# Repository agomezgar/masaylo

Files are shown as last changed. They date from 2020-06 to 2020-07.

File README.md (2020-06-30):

# Robot educativo Masaylo
Estoy intentando desarrollar un robot compatible con Arduino impreso en 3D, Masaylo, de tipo Low-Cost, propulsado por motores DC de los típicos que podemos encontrar en cualquier Aula-Taller de Tecnología.
A medida que progresemos intentaremos dotar al proyecto de una estructura algo más modular y coherente.

## Apariencia general

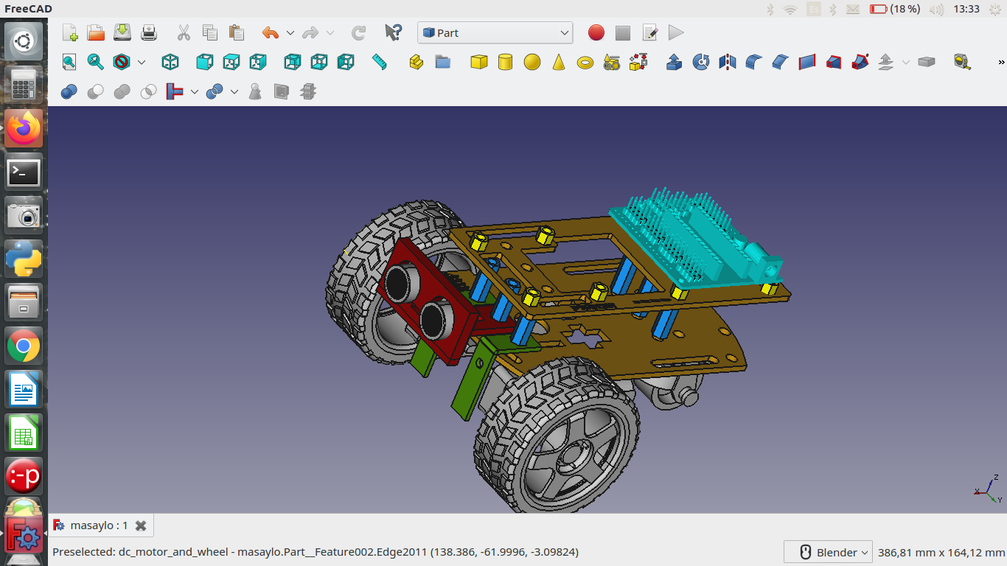
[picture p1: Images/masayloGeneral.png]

Utilizaremos: un Arduino nano con su correspondiente shield de expansión, un módulo L298N para gobernar dos motores DC, una rueda loca de 25x13 cm (o similar), un módulo sensor de ultrasonidos de tipo HC-SR04, dos sensores de infrarrojos de tipo FC-51 y un módulo BT modelo HC-05 o HC-06 que posiblemente habrá que tunear mediante comandos AT (o no; lo fundamental es saber a qué velocidad vamos a comunicarnos con él, y el código original espera que trabajemos a 19200 baudios; si es más cómodo para vosotros, podéis modificar el código para que trabaje a 9600 baudios).

## BOM (Bill of Materials; qué necesitamos)
La lista de objetos impresos en 3D, electrónica y tornillería varia la he dejado en el documento BOM.md que tenéis en la raíz del repositorio

## Instrucciones de montaje
El montaje mecánico del robot es relativamente sencillo. Se incluyen todas las indicaciones en el documento Montaje

## Conexionado/pinout
El Masaylo es lo suficientemente sencillo para que el profe de Tecnología o aficionado a la Robótica elija su propio conexionado, de modo acorde a la Electrónica de que disponga (La única electrónica realmente necesaria es la shield de Arduino, el microcontrolador y el L298N o similar; el resto de sensores son optativos y sustituibles). No obstante, los códigos que se adjuntarán con diversos tutoriales están preparados para el siguiente pinout

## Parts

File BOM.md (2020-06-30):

<h1>BOM (Bill of Materials, lista de materiales necesarios para los legos en english)</h1>
<h2>Piezas impresas en 3D</h2><br>
<table>
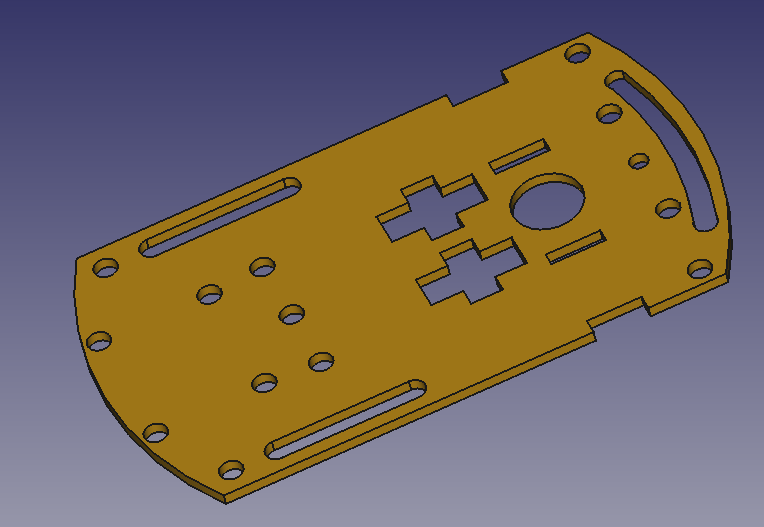
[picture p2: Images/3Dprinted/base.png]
  <tr><td>Base</td><td></td></tr>
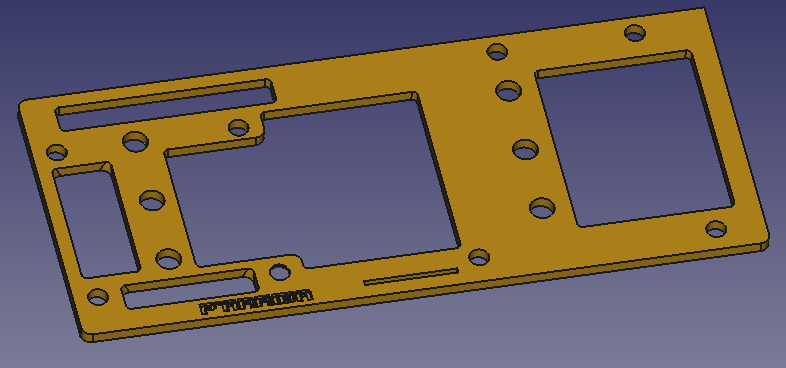
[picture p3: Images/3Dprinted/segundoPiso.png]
  <tr><td>Segundo piso</td><td></td></tr>
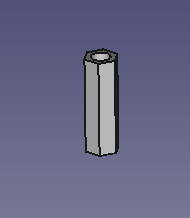
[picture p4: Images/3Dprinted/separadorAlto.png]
  <tr><td>Separadores(pasatornillos) entre base y segundo piso (x6)</td><td></td></tr>
  <tr><td>Separadores (pasatornillos) para shield de Arduino y módulo L298 N (x8)</td><td></td></tr>
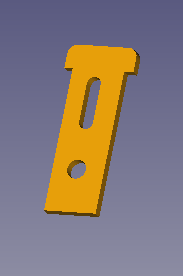
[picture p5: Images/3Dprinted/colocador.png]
    <tr><td>Colocadores/fijadores de motores a base</td><td></td></tr>
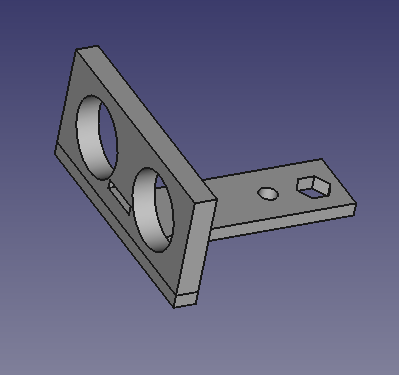
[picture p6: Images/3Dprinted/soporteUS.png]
  <tr><td>Soporte de sensor de ultrasonidos</td><td></td></tr>
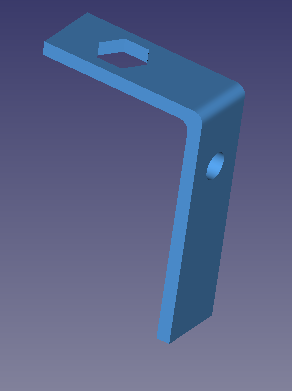
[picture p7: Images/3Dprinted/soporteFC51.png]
  <tr><td>Soporte de sensor de infrarrojos FC51 (si tiras de sensores baratos)</td><td></td></tr>
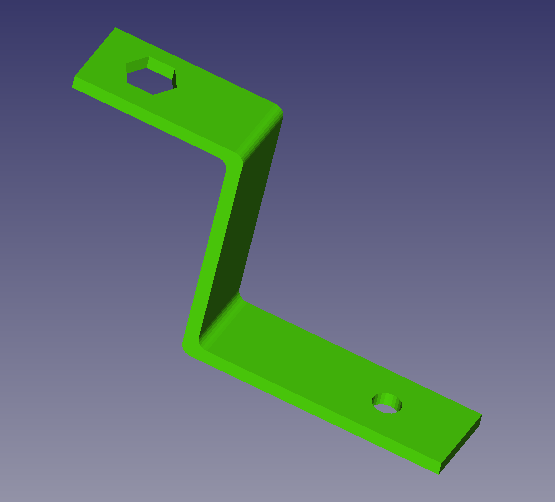
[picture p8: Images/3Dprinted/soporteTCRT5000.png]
  <tr><td>Soporte de sensor de infrarrojos TCRT5000 (si los prefieres a los FC51)</td><td></td></tr>
  </table>
  
  <h2>Electrónica</h2><br>
<table>
  <tr><td colspan="2"><h3>Elementos imprescindibles</h3></td></tr>
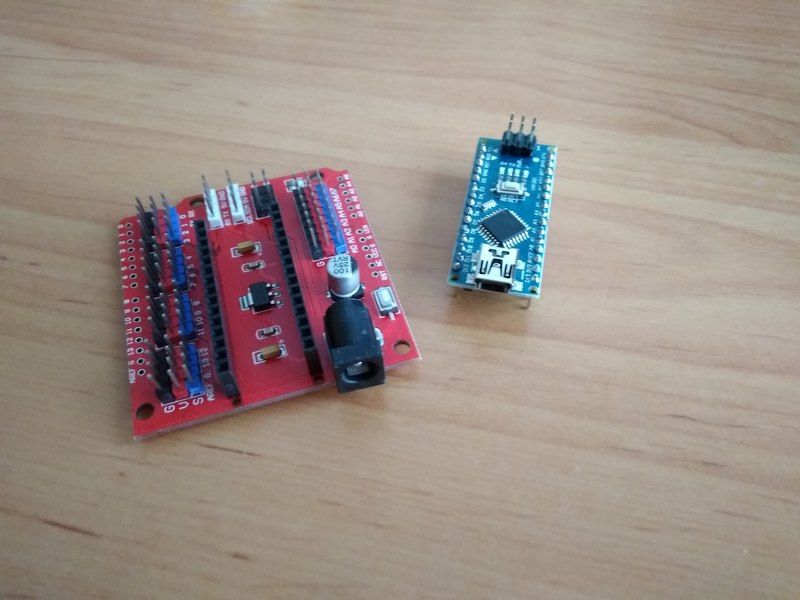
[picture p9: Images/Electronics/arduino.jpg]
  <tr> <td>Arduino nano con shield de expansión v3.0</td><td></td  </tr>
    <tr> <td>Micromotores DC modelo TT con reductora y rueda(x2)</td><td></td  </tr>
  <tr> <td>Módulo L298N para control de motores DC</td><td></td>  </tr>
  <tr> <td>Interruptor de 8 mm o similar</td><td></td>  </tr>
  <tr> <td>Portapilas 4xAA<br> (el portapilas 4xAAA también sirve)<br>Soldar el interruptor al polo positivo del portapilas</td><td></td>  </tr>
      <tr><td colspan="2"><h3>Elementos opcionales</h3></tr>
  <tr> <td>Sensor de ultrasonidos HC-SR04</td><td></td>  </tr>
        <tr> <td>Sensor de infrarrojos TCRT 5000<br>(Primera opción)</td><td></td>  </tr>
        <tr> <td>Sensor de infrarrojos FC51<br>(Más barato, es el que utilizaremos en los tutoriales)</td><td></td>  </tr>
        <tr> <td>Módulo Bluetooth HC05 ó HC06<br>(En aquellos proyectos en que se utilicen, será MUY IMPORTANTE vigilar la velocidad a la que vamos a comunicarnos<br> con dicho módulo, 9600 ó 19200 baudios)</td><td></td>  </tr>

  </table>
  
  <h2>Otros</h2>
  <table>
  <tr><td>Rueda loca universal para coches, de nylon 23x15</td><td> </td></tr>
          <tr> <td>Tornillos y tuercas varios de tipo M3, de 12, 16 y 35 mm</td><td></td>  </tr>
  </table>

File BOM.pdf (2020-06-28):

# Bill of Materials: pinoutMasaylo.fzz

/home/antonio/repositorioGithub/masaylo/pinout/pinoutMasaylo.fzz domingo, junio 28 2020, 11:31:26

## Assembly List

Label | Part Type | Properties
BATT1 4xAA Switchable Battery Pack
| w/Bare Wire
BT1 | Bluetooth HC-06u | paquete THT; row single; variant variant 6; pins 4; espacio
| | entre pines 0.1in (2.54mm)
L298N1 L298N DC motor driver | variant variant 1
M1 | DC Motor
M2 | DC Motor
M3 | fc-51 | paquete THT; editable pin labels false; layout Single Row;
| | variant variant 1; pins 3; espacio entre pines 100mil
M4 | fc-51 | paquete THT; editable pin labels false; layout Single Row;
| | variant variant 1; pins 3; espacio entre pines 100mil
Mod1 | Nano-V3-0-IO-Expansion-
| Adapter | variant variant 1
Nano1 Arduino Nano v2.3 | processor ATmega; variant Arduino Nano v2.3
Parte1

## Shopping List

Amount Part Type | Properties
1 | 4xAA Switchable Battery Pack
| w/Bare Wire
1 | Bluetooth HC-06u | paquete THT; row single; variant variant 6; pins 4; espacio
| | entre pines 0.1in (2.54mm)
1 | L298N DC motor driver | variant variant 1
2 | DC Motor
2 | fc-51 | paquete THT; editable pin labels false; layout Single Row;
| | variant variant 1; pins 3; espacio entre pines 100mil
1 | Nano-V3-0-IO-Expansion-
| Adapter | variant variant 1
1 | Arduino Nano v2.3 | processor ATmega; variant Arduino Nano v2.3
1

Exported with Fritzing 0.7.12- http://fritzing.org

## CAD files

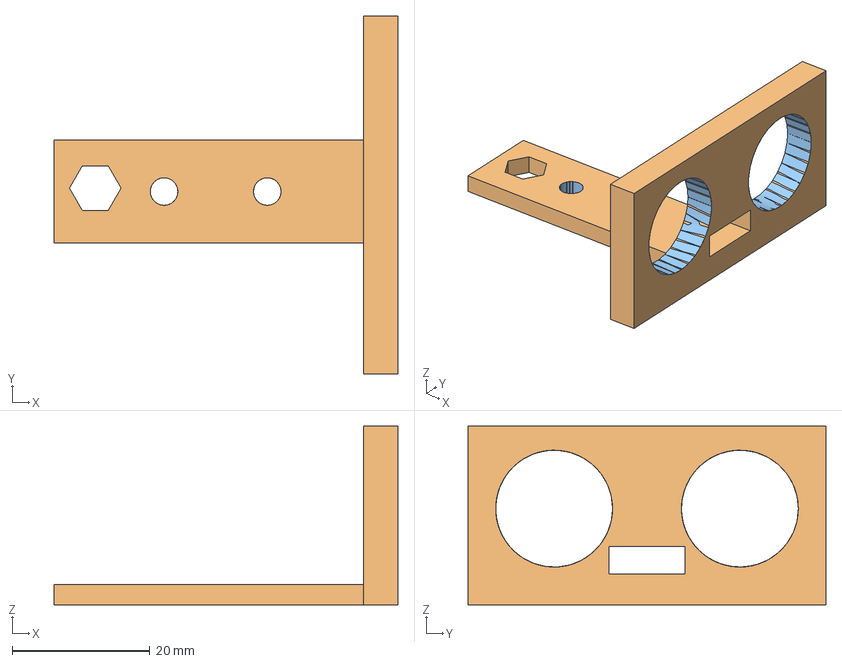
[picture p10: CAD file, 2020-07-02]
FreeCAD/soporteUS.FCStd
50.0 x 52.0 x 26.0 mm
SOPORTEUS
SOPORTEUS (Solid)
SOPORTEUS (Solid) (Meshed)

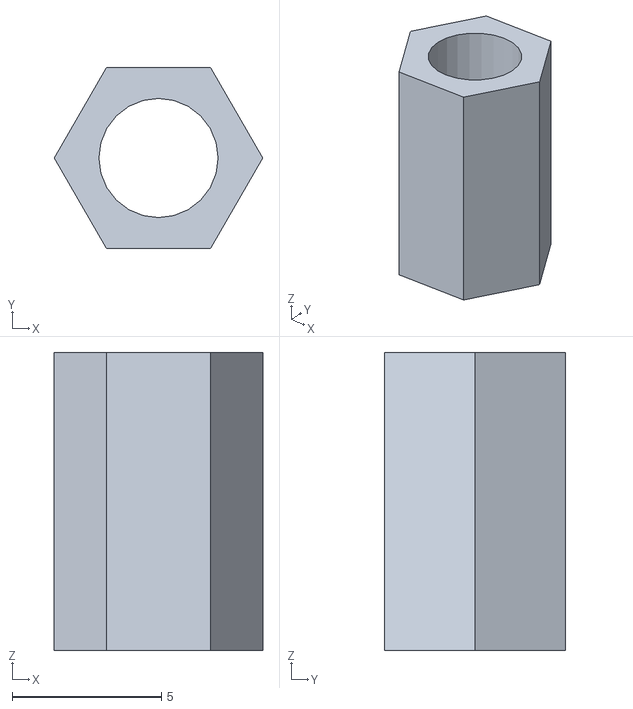
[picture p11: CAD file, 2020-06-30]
STL/separaRueda(x4).stl
7.00 x 6.06 x 10.0

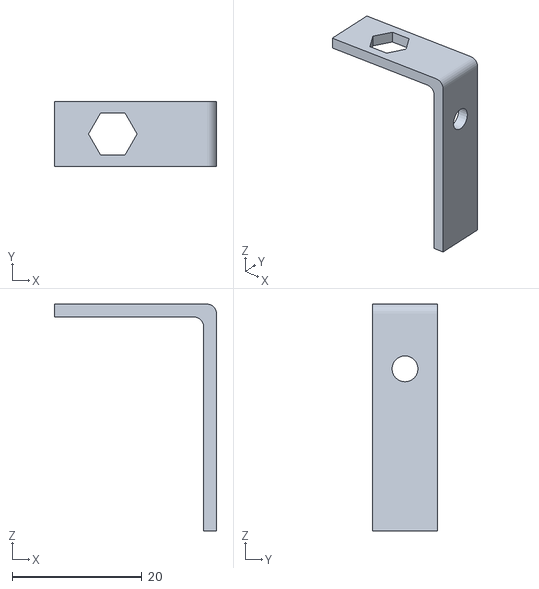
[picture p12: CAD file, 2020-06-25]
STL/SOPORTEIR2.stl
25.0 x 10.0 x 35.0

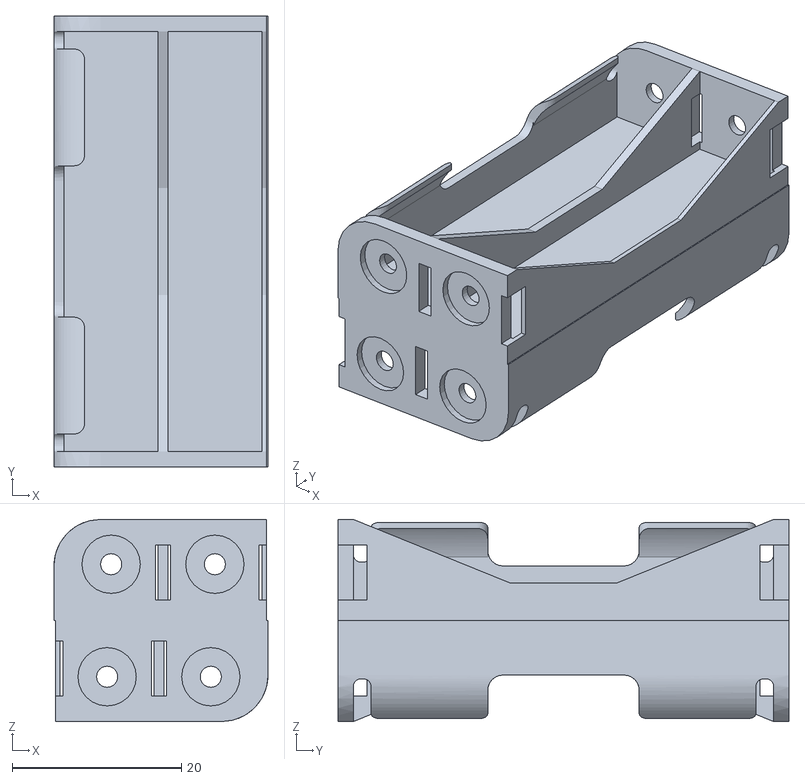
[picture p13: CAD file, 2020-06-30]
FreeCAD/portapilasChapucero.stl
25.3 x 53.3 x 23.9

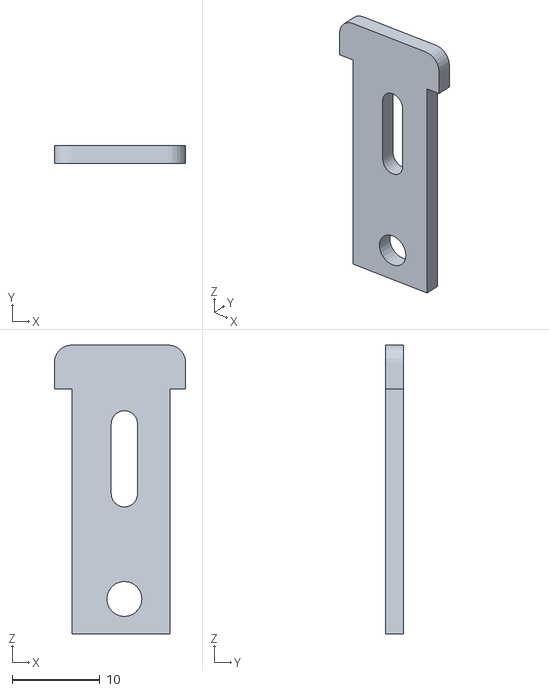
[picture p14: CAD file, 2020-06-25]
STL/colocador(x4).stl
15.0 x 2.00 x 33.0

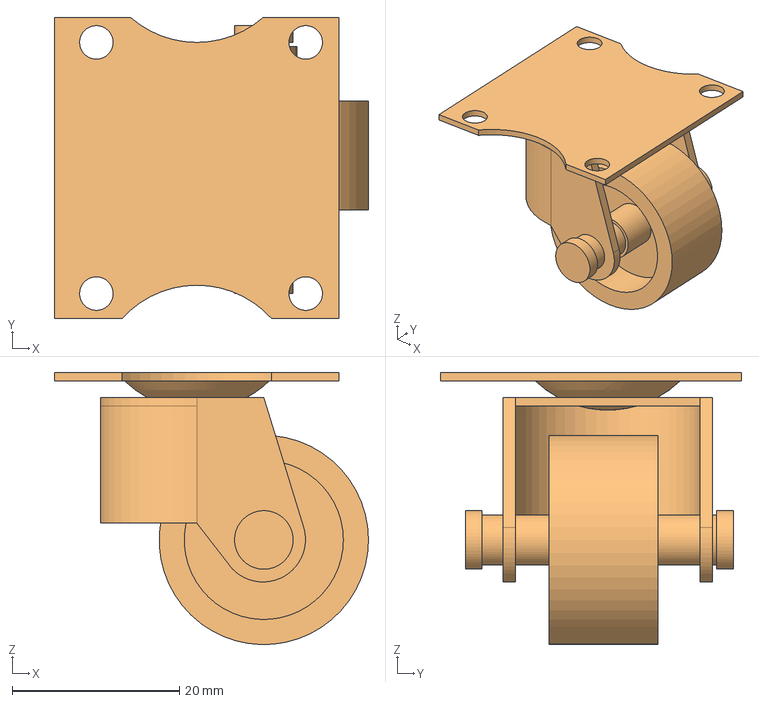
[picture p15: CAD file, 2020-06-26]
FreeCAD/ruedaLoca(inexacta).fcstd
37.5 x 36.0 x 32.5 mm
ruedaLoca25x13
ruedaLoca25x13 (Solid)

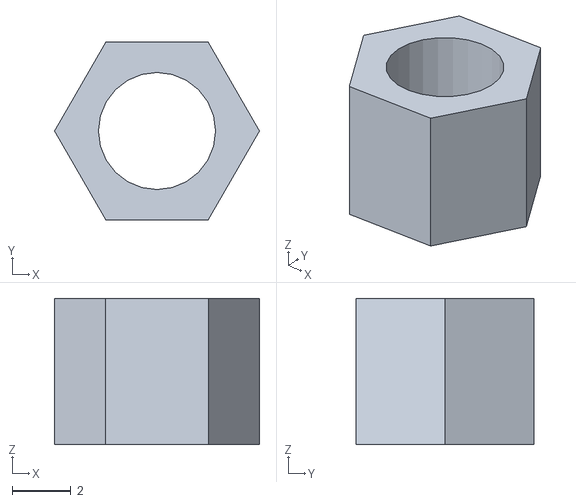
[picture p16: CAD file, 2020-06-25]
STL/separadorSec(x8).stl
7.00 x 6.06 x 5.00

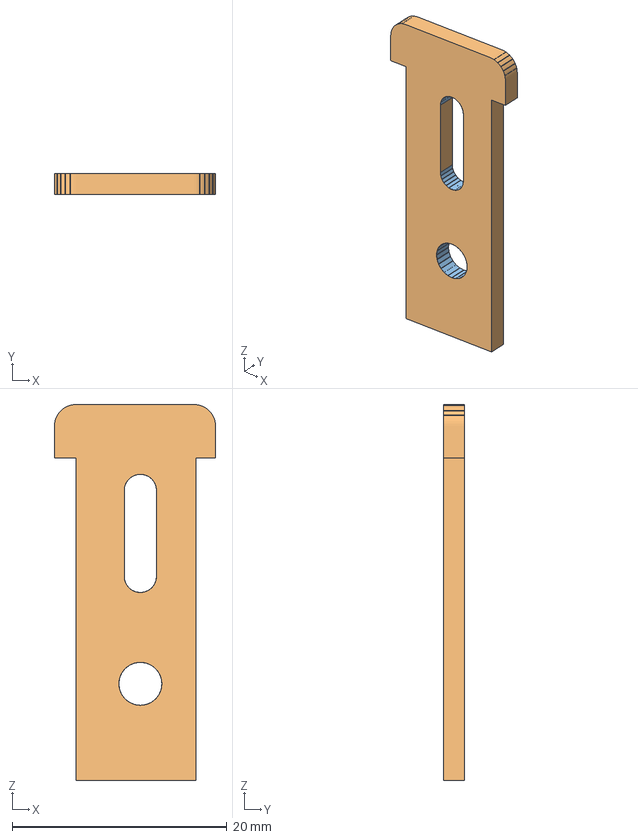
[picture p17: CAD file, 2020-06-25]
FreeCAD/separador.FCStd
15.0 x 2.00 x 35.0 mm
separador
separador (Solid)
separador (Solid) (Meshed)

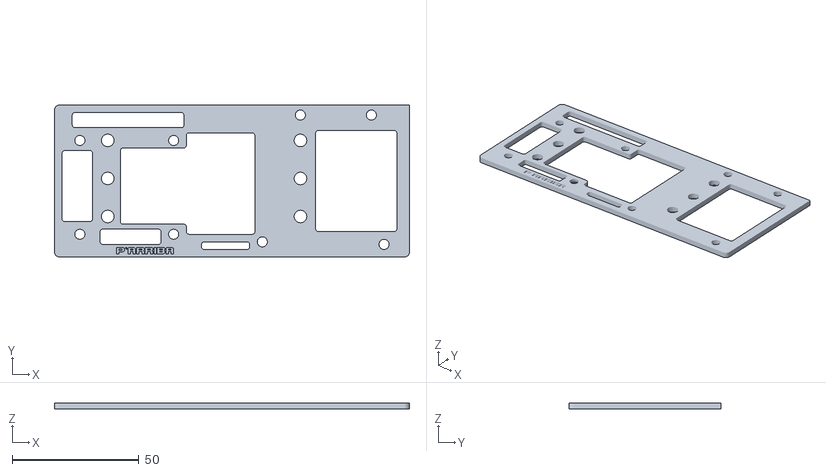
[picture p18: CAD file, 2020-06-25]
STL/SEGUNDOPISO.stl
140.0 x 60.0 x 2.50

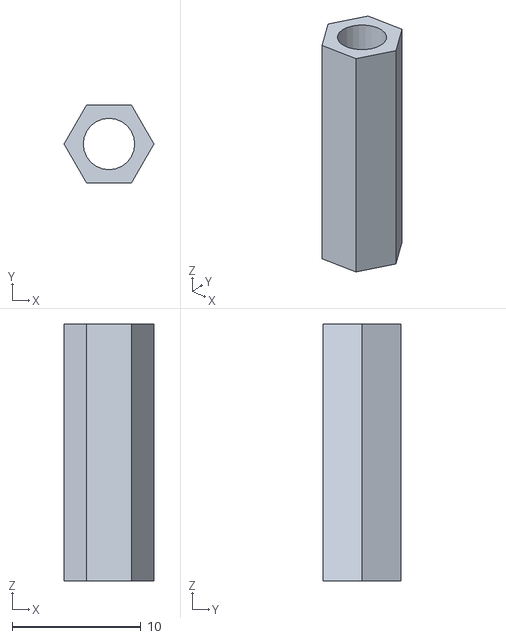
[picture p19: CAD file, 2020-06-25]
STL/SEPARADOR(x6).stl
7.00 x 6.06 x 20.0

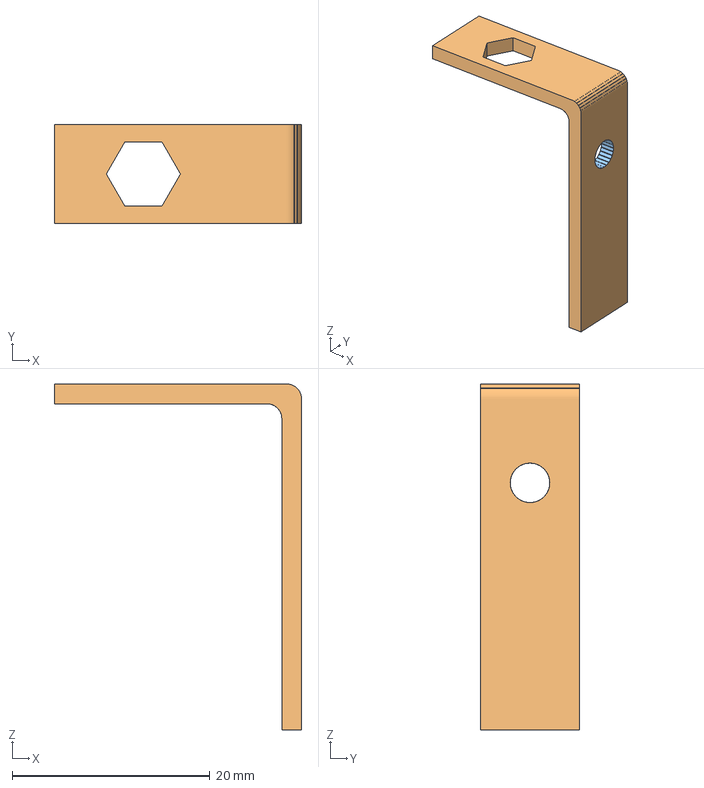
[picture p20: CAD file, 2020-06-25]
FreeCAD/soporteSensorIR2.FCStd
25.0 x 10.0 x 35.0 mm
soporteIR2
soporteIR2 (Solid)
soporteIR2 (Solid) (Meshed)

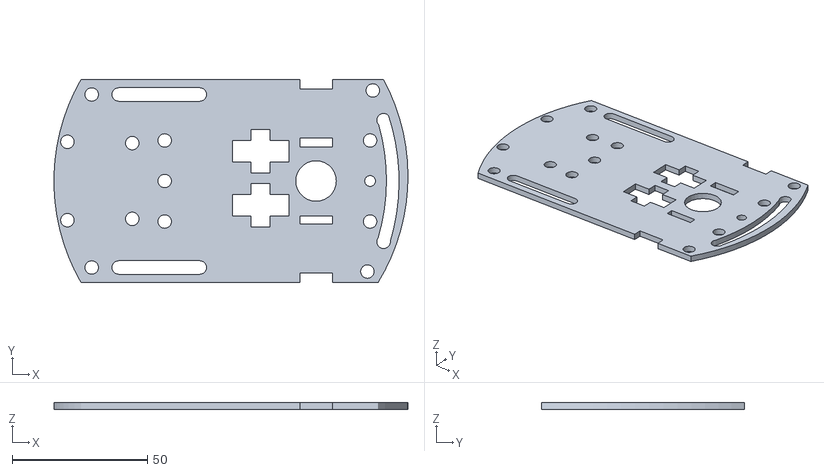
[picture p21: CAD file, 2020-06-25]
STL/BASE.stl
131.0 x 75.0 x 2.50

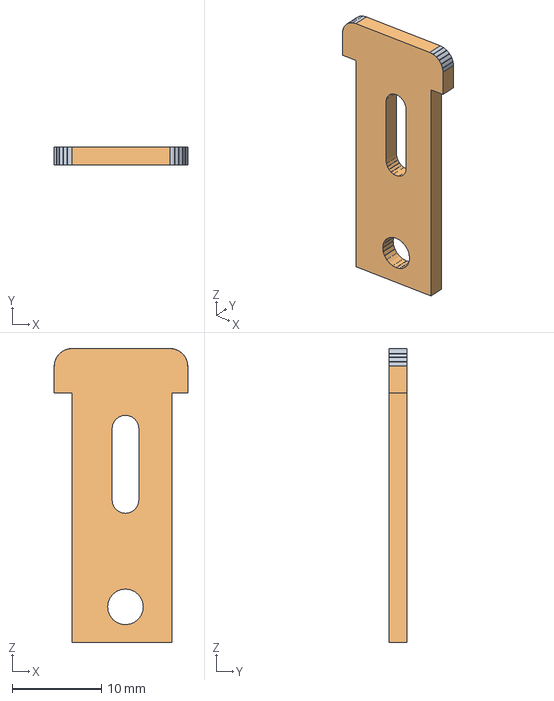
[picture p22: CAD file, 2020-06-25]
FreeCAD/colocador.FCStd
15.0 x 2.00 x 33.0 mm
colocador
colocador (Meshed)

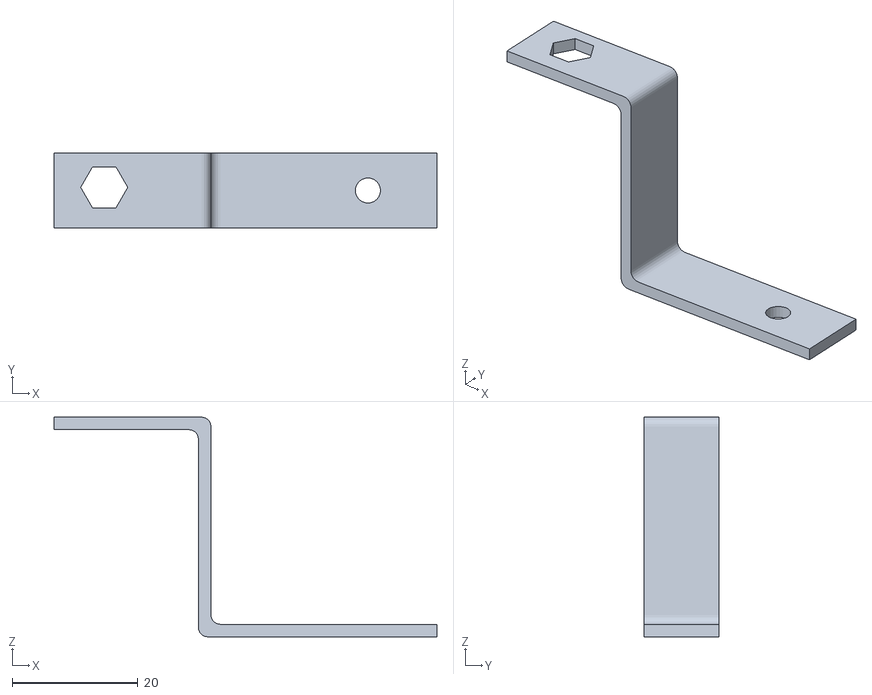
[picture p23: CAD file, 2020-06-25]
STL/soporteIR1.stl
61.0 x 12.0 x 35.0

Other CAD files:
FreeCAD/separaRueda.fcstd
FreeCAD/soporteSensorIR.FCStd
FreeCAD/masaylo.FCStd
FreeCAD/masayloDeprecated.FCStd
STL/SOPORTEUS.stl

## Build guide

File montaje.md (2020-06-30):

<h1>Instrucciones de montaje</h1>
<p>¡Bueno!. ¿Ya has imprimido todas las piezas?. ¿Tienes la electrónica necesaria?. ¿Has acumulado toda la tornillería?. ¡Pues claro que no!. ¡Seguro que falta algo!. Murphy está siempre presente cuando hablamos de Robótica Educativa. De todos modos, no te preocupes. Léete las instrucciones, intenta seguirlas, y cuando algo no salga como estaba previsto, haz lo que hacemos siempre, ¡Improvisa!. ¡Vamos allá!
</p>
<h2> Fijar motores a la base</h2>
<h3>Piezas </h3>
<table>
  <tr><td>Base impresa en 3D</td><td></td></tr>
  <tr><td>Colocadores (x4)</td><td></td></tr>
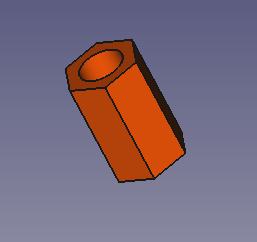
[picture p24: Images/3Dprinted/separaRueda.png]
  <tr><td>Separadores (pasatornillos) para rueda loca (x4)<br>(la pieza en STL se llama "separaRueda(x4)"</td><td></td></tr>
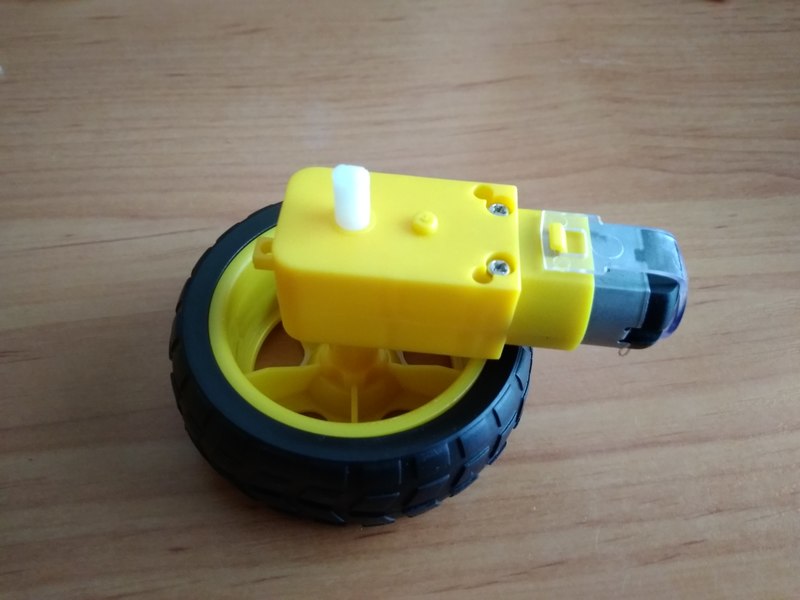
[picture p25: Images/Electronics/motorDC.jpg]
    <tr><td>Motor DC modelo TT con motoreductora y rueda</td><td></td></tr>
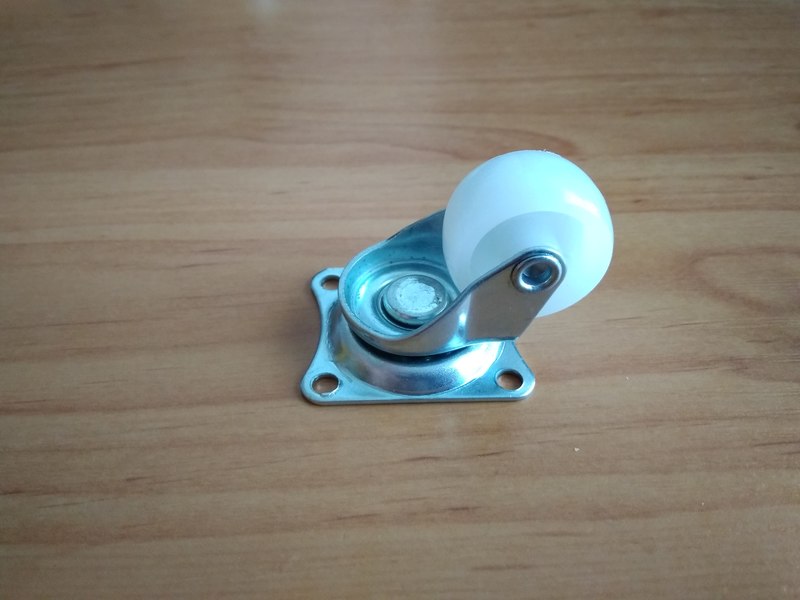
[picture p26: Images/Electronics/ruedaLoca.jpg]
      <tr><td>Rueda loca universal para coches</td><td></td></tr>

  <tr><td>4 tornillos M3x35 mm para atornillar los motores a la base</td></tr>
<tr><td>4 tornillos M3x16 mm para fijar la rueda loca a la base</td></tr>
<tr><td>8 tuercas M3</td></tr>

</table>
</table>
<h3>Proceso </h3>
<p>a) Fijar motores a la base y atornillar, asegurando que el eje mire hacia la parte delantera del robot y los terminales de conexión miren hacia fuera</p>
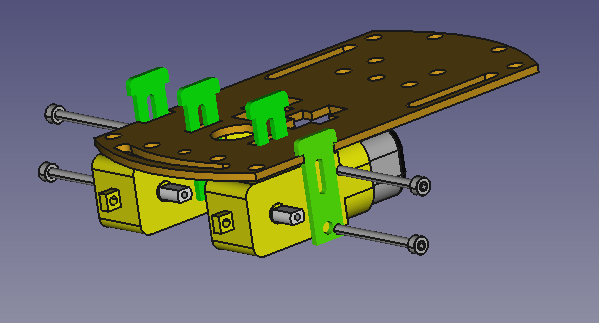
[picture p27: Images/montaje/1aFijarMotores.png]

<p>b) Fijar rueda loca a la base mediante tornillos M3x16 mm a través de los pasadores</p>
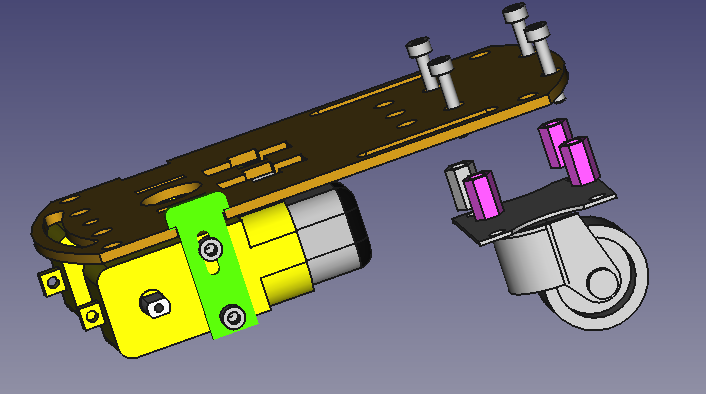
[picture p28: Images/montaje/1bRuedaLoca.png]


<h2> Montar sensores y segundo piso</h2>
<h3>Piezas </h3>
<table>
  <tr><td>Separadores(pasatornillos) entre base y segundo piso(x6)<br>(la pieza en STL se llama "SEPARADOR(x6)"</td><td></td></tr>
  <tr><td>Soporte para sensor de ultrasonidos </td><td></td></tr>
  <tr><td>Soporte para sensor IR (modelo FC-51 ó TCRT5000)(x2)</td><td></td></tr>
    <tr><td>Segundo piso del robot</td><td></td></tr>
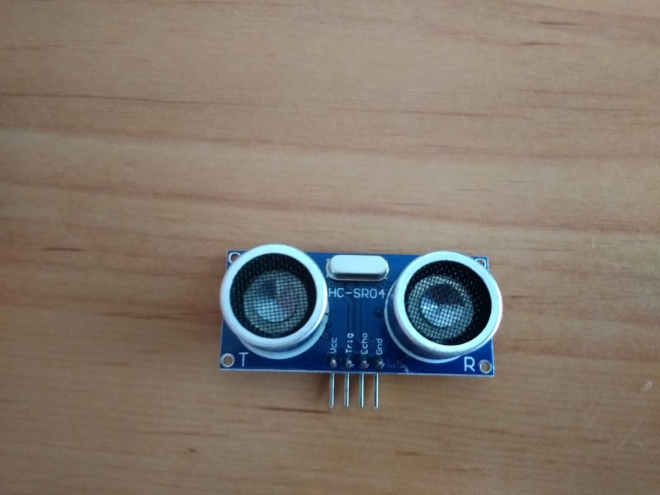
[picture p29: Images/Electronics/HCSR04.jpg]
      <tr><td>Sensor de ultrasonidos HC-SR04</td><td></td></tr>
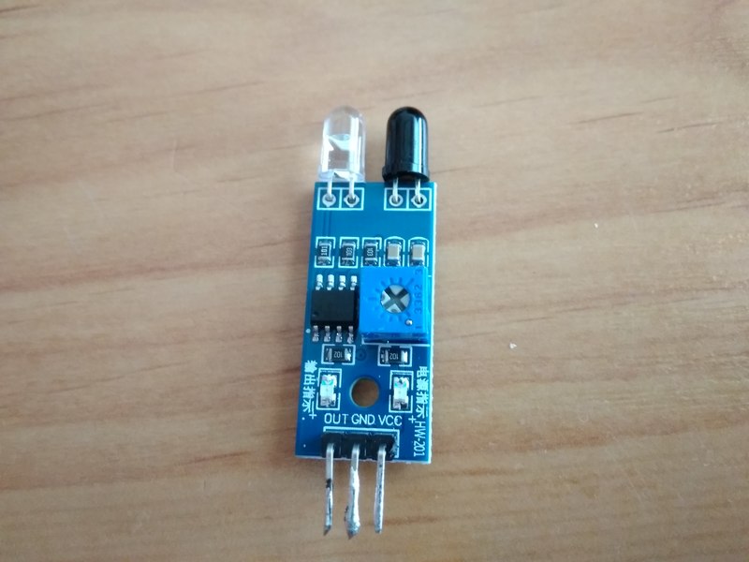
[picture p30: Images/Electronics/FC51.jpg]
  <tr><td>Sensor de infrarrojos (x2) </td><td></td></tr>

  <tr><td>6 tornillos M3x35 mm para fijar el segundo piso a la base</td></tr>
<tr><td>3 tornillos M3x12 mm para atornillar los sensores a sus soportes</td></tr>
<tr><td>9 tuercas M3</td></tr>

</table>
</table>
<h3>Proceso </h3>
<p>a) Montar los sensores en sus soportes. Cada soporte estará atravesado por un separador y se prepararán para colocarlos en la parte delantera del robot</p>
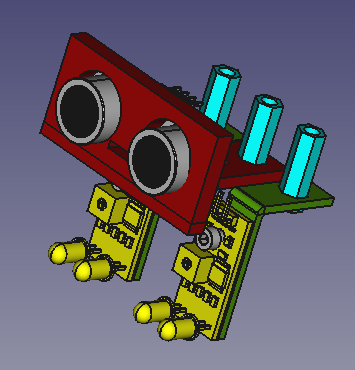
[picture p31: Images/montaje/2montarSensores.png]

<p>b) Atornillar la pieza llamada "Segundo Piso" a la base utilizando los seis separadores</p>
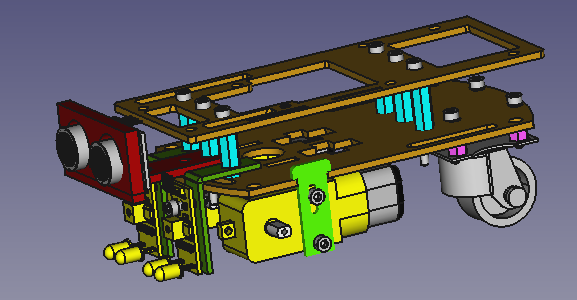
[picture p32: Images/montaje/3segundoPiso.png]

<p><i><b>Nota: Al contrario que con la base, el segundo piso tiene orientación. Hay un pequeño serigrafiado, algo borroso, que pone: "P'ARRIBA". Imagínate para qué sirve. </b></i>
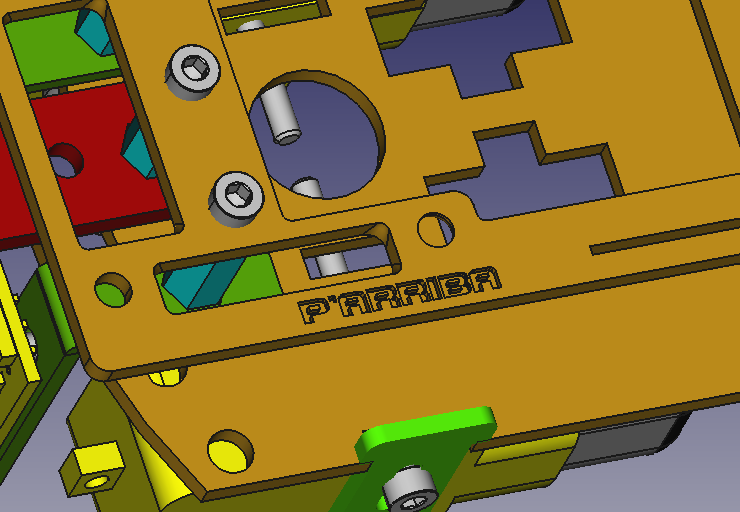
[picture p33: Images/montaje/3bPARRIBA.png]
  

<h2> Fijación de la electrónica</h2>
<h3>Piezas </h3>
<table>
  <tr><td>Separadores para la electrónica<br>(la pieza en STL se llama "separadorSec(x8)"</td><td></td></tr>
  <tr><td>Tarjeta Arduino Nano montada sobre shield de expansión V3 </td><td></td></tr>
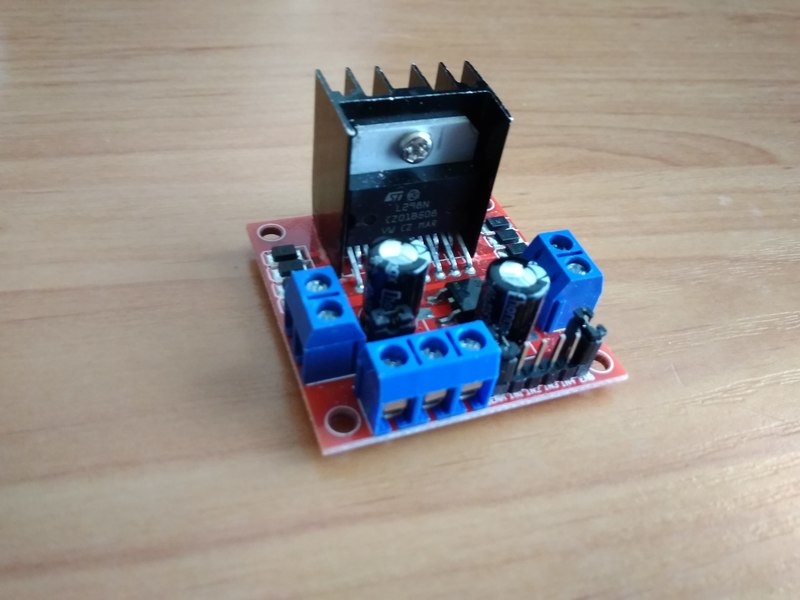
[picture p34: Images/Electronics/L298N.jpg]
  <tr><td>Módulo de control de motores DC L298N</td><td></td></tr>
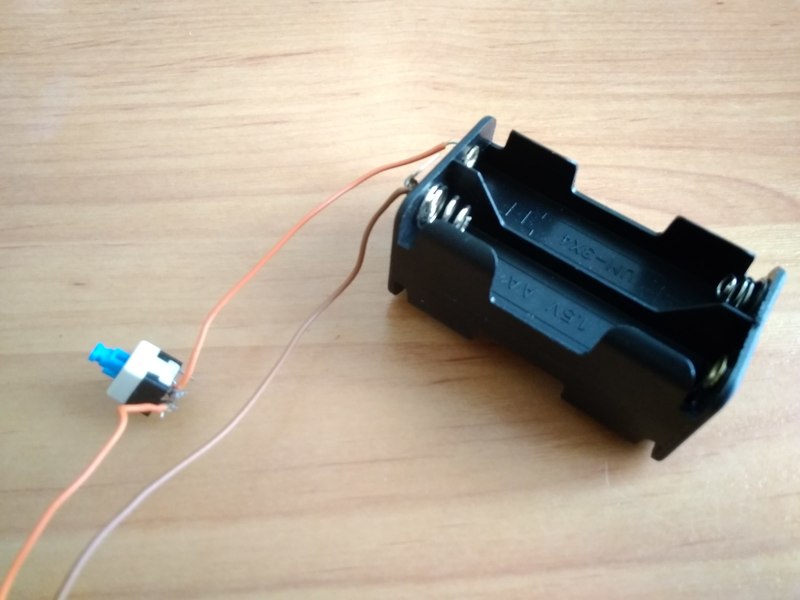
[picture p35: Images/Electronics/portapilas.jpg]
    <tr><td>Portapilas 4xAA con interruptor conectado a cable de positivo</td><td></td></tr>

<tr><td>8 tornillos M3x12 mm para atornillar los módulos al segundo piso</td></tr>
<tr><td>8 tuercas M3</td></tr>

</table>
</table>
<h3>Proceso </h3>
<p>a)Colocar los separadores frente a sus respectivos taladros en el segundo piso </p>
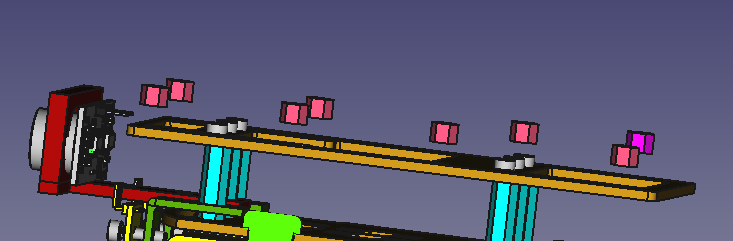
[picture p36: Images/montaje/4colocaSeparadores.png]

<p>b) Fijar ambos circuitos al segundo piso con los tornillos M3x12 mm y sus respectivas tuercas</p>
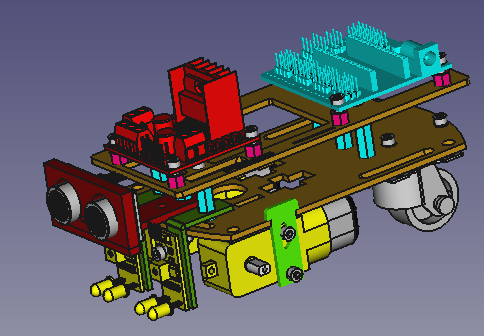
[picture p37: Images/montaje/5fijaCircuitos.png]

<p>Poner el portapilas en el hueco que queda entre la shield de Arduino y el módulo L298 N
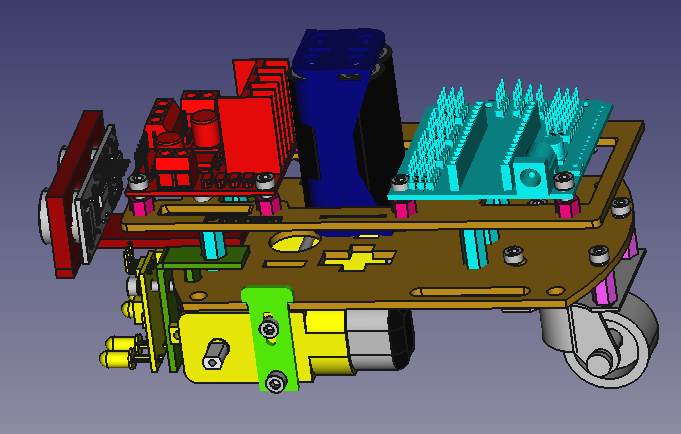
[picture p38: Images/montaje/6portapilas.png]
  
  <h2> Colocamos las ruedas en los motores y, ¡TACHÁÁÁÁÁN!</h2>
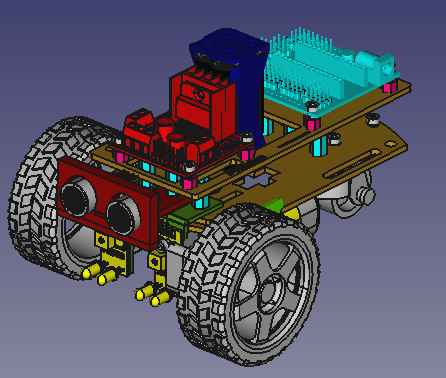
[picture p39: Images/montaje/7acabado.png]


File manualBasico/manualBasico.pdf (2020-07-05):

# MASAYLO

## Robot educativo Open Source Manual básico de montaje y programación

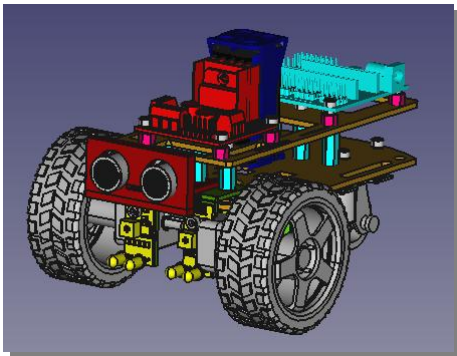
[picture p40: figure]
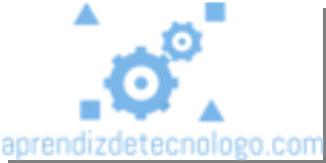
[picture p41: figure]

Antonio Gómez García
M.ª Dolores Nogueras Atance

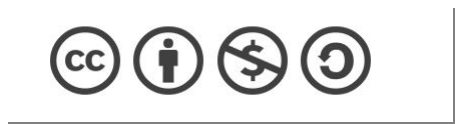
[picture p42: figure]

http://www.aprendizdetecnologo.comhttps://github.com/agomezgar/masaylo

ÍNDICE

## Sumario

ÍNDICE

Ejemplo de control de velocidad de Masaylo mediante funciones y PWM | 43
Trabajo con sensores: detección de distancias con el HC-SR04 | 46
Detección de distancias por ultrasonidos | 46
Función básica para leer distancias con el HC-SR04 | 47
Ejemplo 1: detección de distancias y comunicación vía puerto serie | 48
Ejemplo 2: Masaylo salvaobstáculos | 49
Trabajo con sensores: siguelíneas con sensores de infrarrojos | 54
Características de los sensores de infrarrojos | 54
Conexionado y lectura de sensores infrarrojos | 54
Programación de Masaylo como siguelíneas | 55
Planteamiento: programar a Masaylo como siguelíneas | 57
Comunicación inalámbrica a través del módulo Bluetooth | 61
Principios básicos | 61
Conexionado del módulo BT y velocidad de comunicación | 62
Comunicación de nuestro dispositivo con el módulo BT | 63
Código base de control del Masaylo vía Bluetooth | 65
Programando con AppInventor: MasayloBT.apk | 68
Uso de librerías | 70
La librería Masaylo | 70
Iniciación a la programación con la librería <Masaylo.h>. Movimientos básicos | 70
Métodos implementados para los movimientos básicos | 71
Movimientos de velocidad controlada mediante PWM | 72
Uso del sensor de ultrasonidos. Robot salvaobstáculos | 73
Inicializando los sensores de infrarrojos | 75
Epílogo | 79

Robot educativo Masaylo | 9

# Robot educativo Masaylo

El Masaylo es nuestra propuesta para desarrollar un robot compatible con Arduino impreso en 3D, de tipo Low-Cost, propulsado por los típicos motores DC que podemos encontrar en cualquier Aula-Taller de Tecnología. Masaylo es un robot cuyo diseño se ha liberado bajo licencia LGPL, lo cual quiere decir que las fuentes, códigos, diseños CAD y piezas imprimibles en formato STL pueden ser compartidos libremente por la comunidad bajo los términos que indica dicha licencia. Las piezas que componen propiamente a Masaylo han sido íntegramente diseñadas con el software Open Source FreeCAD.

## Apariencia general

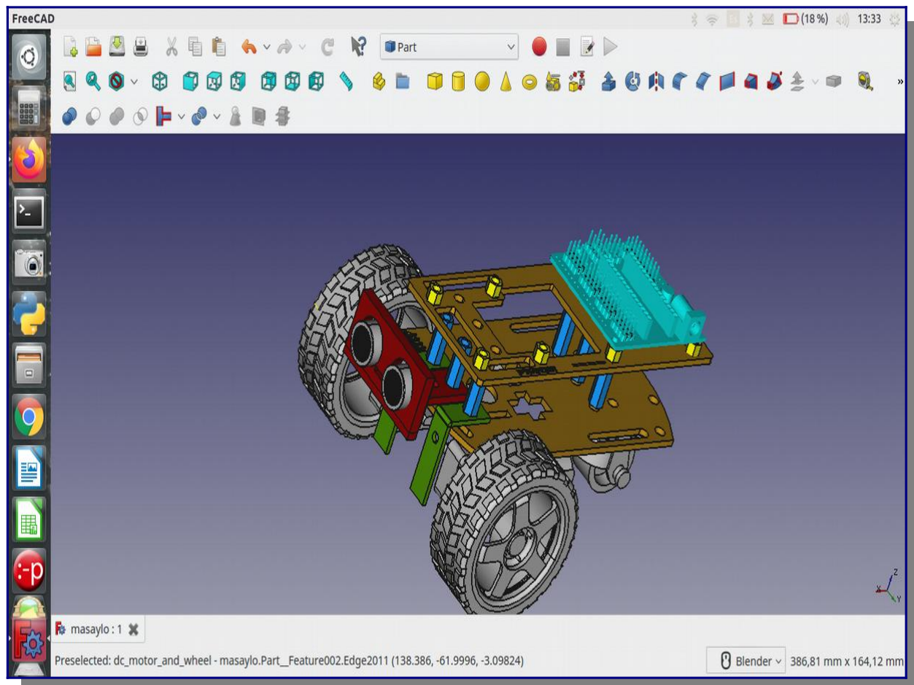
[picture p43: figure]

Utilizaremos: un Arduino nano con su correspondiente shield de expansión, un módulo L298N para gobernar dos motores DC, una rueda loca de 25x13 cm (o similar), un módulo sensor de ultrasonidos de tipo HC-SR04, dos sensores de infrarrojos de tipo FC-51 y un módulo BT modelo HC-05 o HC-06 que posiblemente habrá que tunear mediante comandos AT (o no; lo fundamental es saber a qué velocidad vamos a comunicarnos con él, y el código original espera que trabajemos a 19200 baudios; si es más cómodo para el lector, puede modificarse el código para que trabaje a 9600 baudios).

## Sobre los códigos mostrados en el manual

Todos los códigos e imágenes mostrados en el presente manual son de libre uso para el lector bajo la licencia Open Source correspondiente, y están en el repositorio de los autores: https://github.com/agomezgar/masaylo

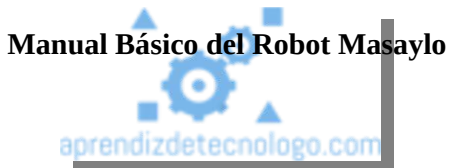
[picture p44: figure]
Manual Básico del Robot Masaylo

### 10 Piezas, tornillería y circuitos necesarios

# Piezas, tornillería y circuitos necesarios

## Piezas impresas en 3D

Pieza impresa en 3D | Imagen

Base

Segundo piso

Separadores(pasatornillos) entre base y segundo piso (x6)

Separadores (pasatornillos) para shield de Arduino y módulo L298 N (x8)

Colocadores/fijadores de motores a base

Soporte de sensor de ultrasonidos

Piezas, tornillería y circuitos necesarios | 11
Pieza impresa en 3D | Imagen

Soporte de sensor de infrarrojos FC51 (si tiras de sensores baratos)

Soporte de sensor de infrarrojos TCRT5000 (si los prefieres a los FC51)

## Electrónica

Electrónica imprescindible

Arduino nano con shield de expansión v3.0

Micromotores DC modelo TT con reductora y rueda(x2)

Módulo L298N para control de motores DC

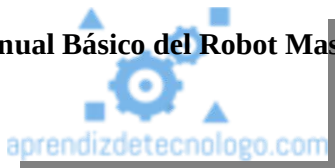
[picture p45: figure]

### 12 Piezas, tornillería y circuitos necesarios

Electrónica imprescindible

Interruptor de 8 mm o similar

Portapilas 4xAA (el portapilas 4xAAA también sirve) Soldar el interruptor al polo positivo del portapilas

Sensores opcionales

Sensor de ultrasonidos HC-SR04

Sensor de infrarrojos TCRT 5000 (Primera opción)

Sensor de infrarrojos FC51 (Más barato, es el que utilizaremos en los tutoriales)

Piezas, tornillería y circuitos necesarios | 13

Sensores opcionales

Módulo Bluetooth HC05 ó HC06
(En aquellos proyectos en que se utilicen, será MUY IMPORTANTE vigilar la velocidad a la que vamos a comunicarnos con dicho módulo, 9600 ó 19200 baudios) No es exactamente un sensor, sino un módulo de comunicación inalámbrica, pero forma parte igualmente de la electrónica opcional

## Otros

Descripción | Imagen

Rueda loca universal para coches, de nylon 23x15 (Nota: en un futuro, se intentará proporcionar una solución alternativa mediante impresión 3D)

Tornillos y tuercas varios de tipo M3, de 12, 16 y 35 mm

### 14 Instrucciones de montaje

# Instrucciones de montaje

Según nuestra experiencia, es muy común que a la hora de iniciar cualquier proyecto, por más esfuerzos que haga el estudiante, fallará algo, o no se dispondrá de alguna pieza o herramienta, o no es exactamente del modelo especifica. ¡No pasa nada!. Murphy está siempre presente cuando hablamos de Robótica Educativa. No hay que preocuparse. Intentaremos seguir las instrucciones, y cuando algo no salga como estaba previsto, haremos lo que hacemos siempre, ¡improvisar!. ¡Vamos allá!

## Fijar motores a la base

Piezas

Nombre | Imagen

Base impresa en 3D

Colocadores (x4)

Separadores (pasatornillos) para rueda loca (x4) (la pieza en STL se llama "separaRueda(x4)"

Motor DC modelo TT con motoreductora y rueda

Instrucciones de montaje | 15
Nombre | Imagen

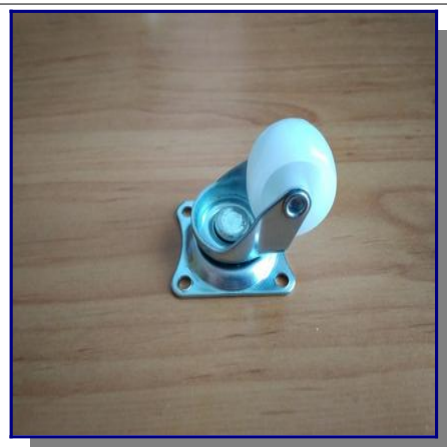
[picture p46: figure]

Rueda loca universal para coches

4 tornillos M3x35 mm para atornillar los motores a la base 4 tornillos M3x16 mm para fijar la rueda loca a la base
8 tuercas M3

Proceso

a) Fijar motores a la base y atornillar, asegurando que el eje mire hacia la parte delantera del robot y los terminales de conexión miren hacia fuera
b) Fijar rueda loca a la base mediante tornillos M3x16 mm a través de los pasadores

### 16 Instrucciones de montaje

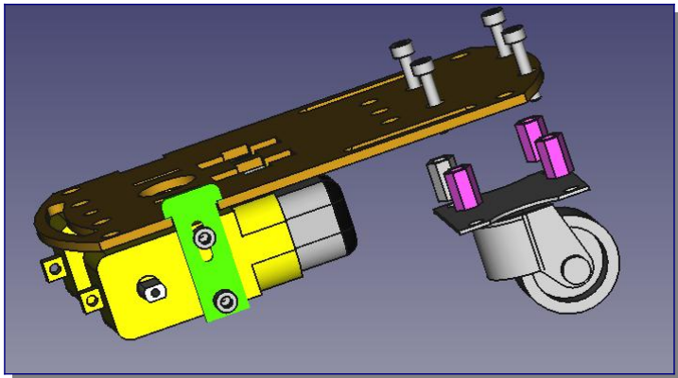
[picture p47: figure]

## Montar sensores y segundo piso

Piezas

Nombre | Imagen

Separadores(pasatornillos) entre base y segundo piso(x6) (la pieza en STL se llama "SEPARADOR(x6)"

Soporte para sensor de ultrasonidos

Soporte para sensor IR (modelo FC-51 ó TCRT5000)(x2)

Instrucciones de montaje | 17
Nombre | Imagen

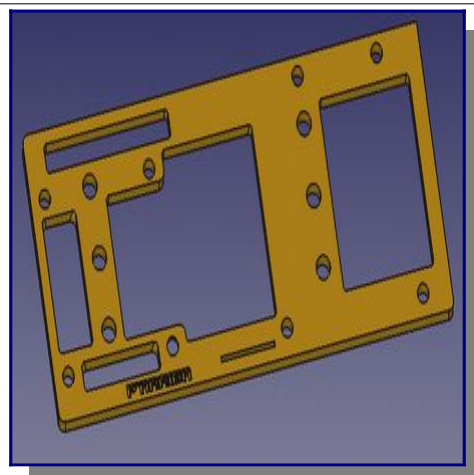
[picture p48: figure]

Segundo piso del robot

Sensor de ultrasonidos HC-SR04

Sensor de infrarrojos (x2)

6 tornillos M3x35 mm para fijar el segundo piso a la base
3 tornillos M3x12 mm para atornillar los sensores a sus soportes
9 tuercas M3
Proceso
a) Montar los sensores en sus soportes. Cada soporte estará atravesado por un separador y se prepararán para colocarlos en la parte delantera del robot

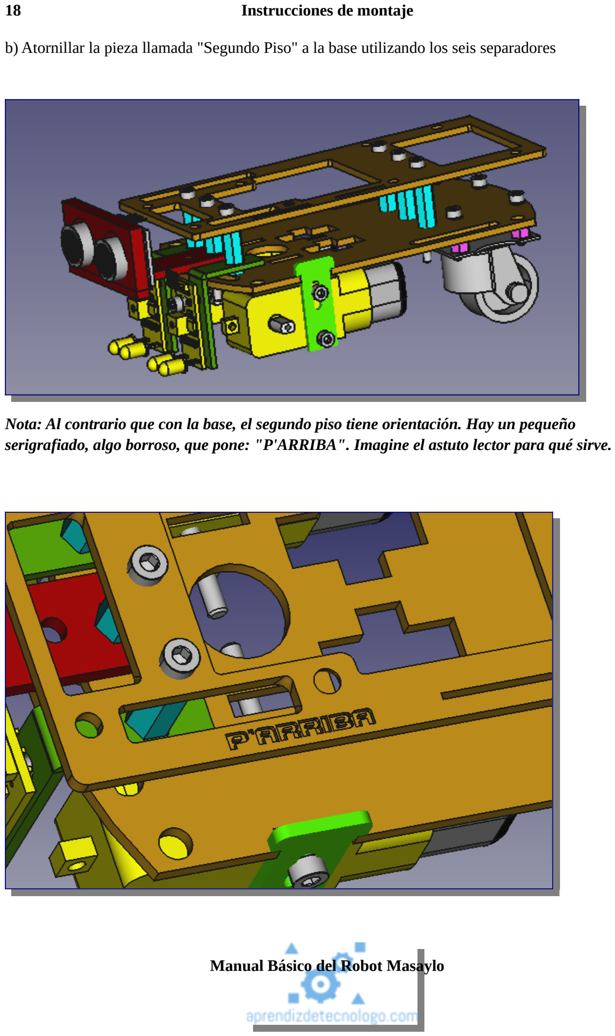
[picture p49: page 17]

### 18 Instrucciones de montaje

b) Atornillar la pieza llamada "Segundo Piso" a la base utilizando los seis separadores

Nota: Al contrario que con la base, el segundo piso tiene orientación. Hay un pequeño serigrafiado, algo borroso, que pone: "P'ARRIBA". Imagine el astuto lector para qué sirve.

Instrucciones de montaje | 19

## Fijación de la electrónica

Piezas

Separadores para la electrónica (la pieza en STL se llama "separadorSec(x8)"

Tarjeta Arduino Nano montada sobre shield de expansión V3

Módulo de control de motores DC L298N

### 20 Instrucciones de montaje

Separadores para la electrónica (la pieza en STL se llama "separadorSec(x8)"

Portapilas 4xAA con interruptor conectado a cable de positivo

8 tornillos M3x12 mm para atornillar los módulos al segundo piso
8 tuercas M3
Proceso
a)Colocar los separadores frente a sus respectivos taladros en el segundo piso

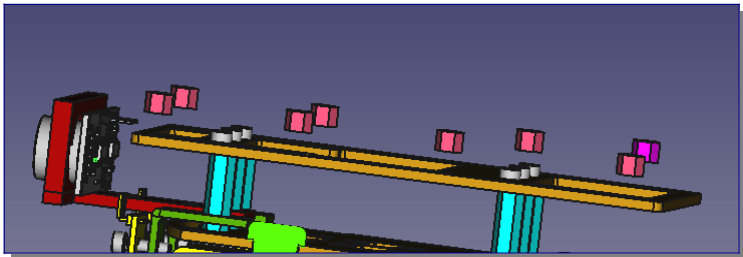
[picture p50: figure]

b) Fijar ambos circuitos al segundo piso con los tornillos M3x12 mm y sus respectivas tuercas

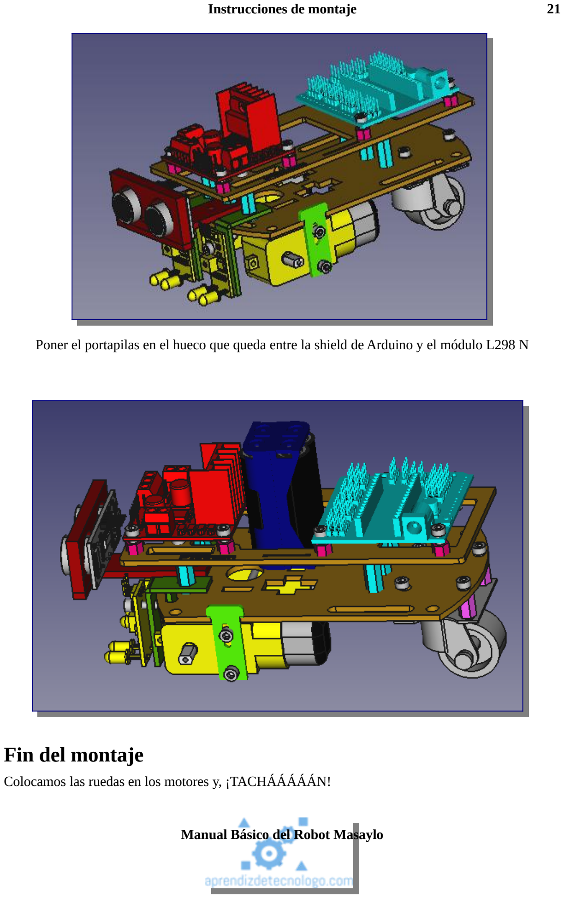
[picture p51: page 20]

Instrucciones de montaje | 21

Poner el portapilas en el hueco que queda entre la shield de Arduino y el módulo L298 N

## Fin del montaje

Colocamos las ruedas en los motores y, ¡TACHÁÁÁÁÁN!

### 22 Instrucciones de montaje

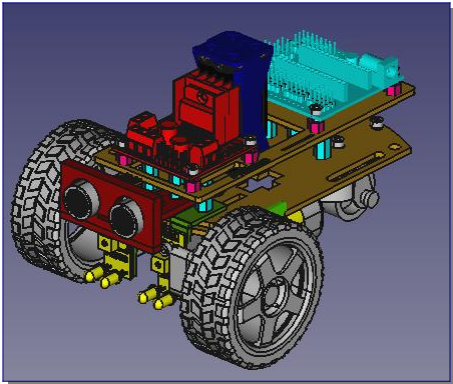
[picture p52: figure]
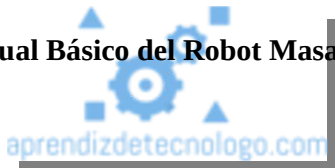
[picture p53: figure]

Conexionado (pinout) de Masaylo | 23

# Conexionado (pinout) de Masaylo

## Algunos matices a tener en cuenta

Masaylo es un robot educativo cuyo único fin es ayudar a comprender al estudiante o aficionado algunos de los aspectos básicos de la Robótica y el Automatizado y Control Electrónico que hoy en día se trabajan en múltiples unidades didácticas dentro de materias relacionadas con la Tecnología tanto en Educación Secundaria como en Primaria.
Hoy en día hay muchos y muy bien diseñados robots educativos relacionados con Arduino y con características Open Source (Escornabot y OttoDIYs son dos de los primeros ejemplos que vendrán a la mente de muchos lectores). Si nos hemos atrevido a presentar nuestro propio proyecto a este respecto es porque creemos que hay, entre otros, dos puntos a su favor:
- Es un robot de muy bajo coste, a la par que sólido y de construcción muy simple.
- Se propulsa mediante motores DC de los más comúnmente utilizados en cualquier taller de Tecnología de cualquier instituto de Educación Secundaria.
El uso de motores DC, comúnmente más fáciles de encontrar que los stepper y los servomotores de aeromodelismos como los SG-90, son además muy baratos y mucho más sólidos que sus antagonistas. Pero su principal ventaja es que el adolescente o niño que empiece a aprender a programar un robot como Masaylo comprende mucho mejor el control de un motor DC que el de un motor paso a paso o un servomotor, que exigen el uso de pulsos de tipo PWM o enviar secuencias de control a través de varias patillas del microcontrolador. Un motor DC, en cambio, gira con mucha potencia en un sentido o en otro dependiendo de la polaridad de la alimentación que se le proporcione.

## Electrónica imprescindible y circuitos opcionales

Como ya se ha comentado, Masaylo necesita únicamente una tarjeta de control de tipo Arduino Nano insertada en una shield de expansión y un módulo de control de tipo puente en H como el L298N para controlar los motores de corriente continua (además, por supuesto, de dichos motores). Los sensores de ultrasonidos y de infrarrojos, además del módulo Bluetooth que se proponen, son no sólo opcionales, sino incluso sustituibles por otros sensores o actuadores a gusto del programador.
Empezaremos aprendiendo a programar las salidas digitales de Arduino mediante el uso de funciones para introducir en el robot la secuencia de movimientos que deseamos. A partir de ahí, todo lo que venga después dependerá exclusivamente de nuestra imaginación.
El Masaylo está diseñado para un portapilas de 4 pilas tipo AA, pero incluso este aspecto constructivo queda a disposición de la imaginación y la capacidad de improvisación del estudiante que se disponga a llevar a cabo el proyecto.

Conexionado (pinout) de Masaylo | 25

## Pines de Arduino

El programador algo más experto puede optar por su propia elección de pines, sea por comodidad o por que le parezca más acertada. Al utilizar, en el planteamiento de esta primera versión del robot, únicamente pines digitales, esto no debería plantear ningún problema. No obstante, en los próximos capítulos, los códigos que incluiremos harán referencia a este pinout:

ELEMENTO DE CONTROL | PIN/PINES DIGITALES
Motor izquierdo | 5 y 6
Motor derecho | 9 y 10
Sensor infrarrojo izquierdo | 2
Sensor infrarrojo derecho | 3
Sensor de ultrasonidos HC-SR04 | Trigger→7 Echo→8
Módulo de comunicaciones Bluetooth | Tx→12 Rx->13

Quedan algunos pines sin usar (0 y 1 normalmente se obvian porque son los que utiliza el ordenador para comunicarse con Arduino). Queda a la imaginación del lector posibles usos para ellos.

## Conexión de la alimentación

Quizás sorprenda un poco al inexperto que, a diferencia de los montajes a que estamos acostumbrados, el polo positivo de la alimentación no se conecta a +5V ni al pin Vin de la Arduino, sino a la patilla +12 V del L298N. Esto se explicará en el próximo capítulo. Quede también MUY CLARO QUE LAS TIERRAS (PINES GND) DE AMBOS CIRCUITOS, ARDUINO Y L298N, DEBEN ESTAR INTERCONECTADAS ENTRE SÍ.

### 26 Alimentación de Masaylo. Uso del L298N

# Alimentación de Masaylo. Uso del L298N

## ¿Por qué no podemos controlar motores DC desde Arduino?

Uno de los mayores escollos que nos encontramos en Robótica Educativa, cuando trabajamos en centros educativos, es el tema de la movilidad del robot. Por diversas razones, el gobierno de un motor desde un microcontrolador se hace normalmente muy difícil, dado que la propia naturaleza de estos dispositivos, basados en la excitación de bobinas mediante electricidad, hace que absorban suficiente corriente eléctrica como para “aturdir” al microchip que intenta manejarlos.
El circuito de la siguiente imagen, por ejemplo, no es funcional. La primera intención del principiante es conectar el motor a dos pines digitales de Arduino (4 y 9 en nuestro ejemplo), con intención de controlarlo alternando “1” y “0” lógicos (esto es, conectando los bornes del motor a +5 V y tierra para lograr el giro del motor en el sentido correspondiente). Pronto se desengañará y comprobará que el motor no obedece.

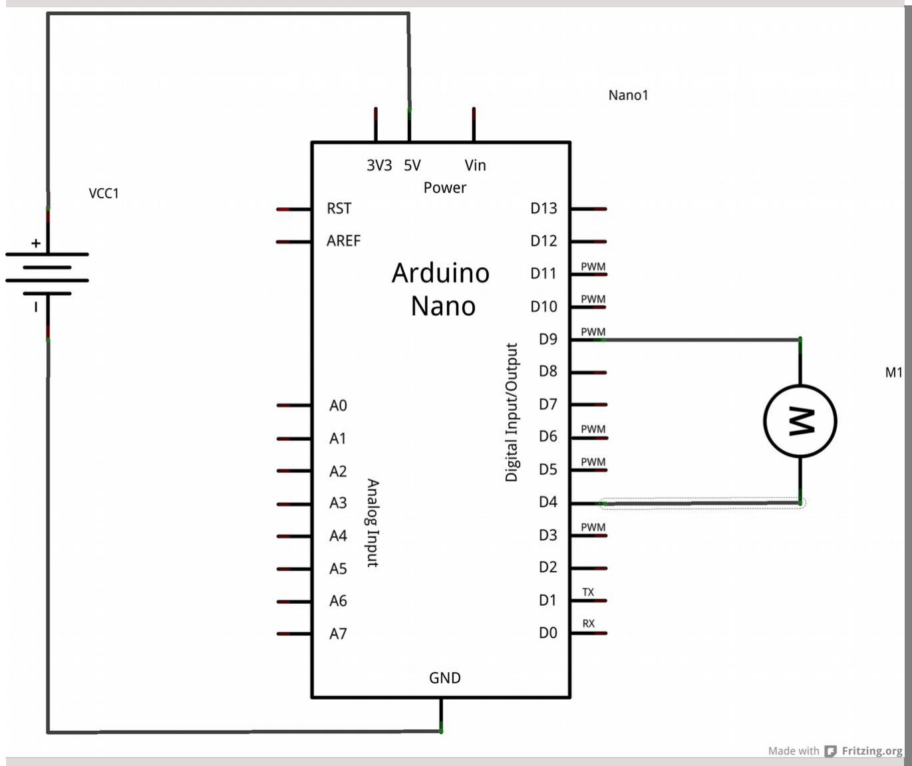
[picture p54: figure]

Un intento de gobierno directo de un motor DC desde un microcontrolador nunca funcionará.

Alimentación de Masaylo. Uso del L298N | 27

¿Por qué?. Si nuestra tarjeta asocia los estados “HIGH” y “LOW” a 5 V y 0 V, respectivamente, el motor debería moverse. Sin embargo, olvidamos que lo que mueve al motor no es la tensión, sino la intensidad. Y los microcontroladores como los que contiene Arduino pueden mantener las tensiones establecidas siempre que no se les pida una intensidad de corriente por encima de unos pocos miliamperios, muy por debajo de lo que necesita un motor de corriente continua para empezar a funcionar. ¿El resultado? No hay movimiento, y muy probablemente la tarjeta se bloqueará.

Este problema, como todos los demás, tiene diferentes soluciones. Una consiste en buscar otro tipo de motores, como los stepper o “paso a paso”, con menos exigencias a este respecto. Otra consiste en utilizar relés (tampoco es muy funcional por diversas razones). La que nos ocupa en este caso consiste en utilizar una alimentación separada de Arduino (esto es, otra pila o batería), eso sí, con una tierra común (ambos polos negativos deben estar conectados entre sí) y un circuito que hará de intermediario entre la tarjeta y dicha alimentación. Este tipo de circuitos utiliza transistores según el modelo denominado “puente en H”, como es el ejemplo del L293DNE, sobre el que ya escribimos hace algunos años sobre su posible uso con Arduino. (http://www.aprendizdetecnologo.com/index.php/publicaciones/53-control-de-motores-de-corriente-continua-con-puentes-de-transistores-el-circuito-293dne) Dicho circuito en el caso de Masaylo es el L298N.

## El circuito L298N

Elegimos este modelo por su accesibilidad comercial (puede conseguirse muy fácilmente), muy bajo precio y por su adaptabilidad a múltiples condiciones de trabajo en tensiones y modulación de velocidad.

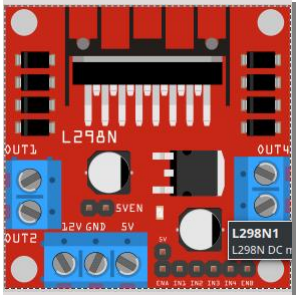
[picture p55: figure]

L298N (módulo creado para Fritzing)

### 28 Alimentación de Masaylo. Uso del L298N

Hay mucha bibliografía en español sobre las características de este módulo (nosotros
recomendamos en particular un excelente artículo sobre el particular en la web de Luis Llamas, (https://www.luisllamas.es/arduino-motor-corriente-continua-l298n/) www.luisllamas.es), así que no creemos posible añadir nada útil al respecto. Sólo resaltaremos estos puntos:
- El propósito general de este tipo de circuitos es recibir en sus entradas señales lógicas de 5 V que repetirán en sus respectivas salidas con la alimentación que se les da (hasta 35 V), solucionando así el problema de alimentar correctamente a los motores.
- Admite alimentaciones de 6 V hasta 12 V con el jumper regulador (nuestro caso), y hasta 35 V si quitamos dicho jumper.
- El uso de ENA y ENB si quitamos sus jumper permitiría la modulación de la velocidad del motor mediante impulsos PWM, previa desinstalación del mismo jumper regulador(no lo necesitaremos).
- El borne serigrafiado como +5V funciona como una salida de tensión con los jumper puestos, pero si los quitáramos tendríamos que proporcionar dicha tensión para alimentar la lógica del circuito.
- Por el propio diseño del circuito, entre la tensión que proporcionemos y la que llegue a los motores DC se producirá una pérdida de alrededor de 1,5 V.
Por otro lado, la lógica de conexionado para gobernar hasta dos motores de corriente continua es extremadamente intuitiva:
ENTRADA | SALIDA
IN1 | OUT1
IN2 | OUT2
IN3 | OUT3
IN4 | OUT4

Como ya se ha comentado en apartados anteriores, es posible que alguno o ambos motores funcionen al revés de como se les indica (esto es, que giren en sentido antihorario cuando se les pide sentido horario, o al revés). Bastará con intercambiar las correspondientes patillas INx o OUTx (lo que resulte más sencillo).

## Alimentación de Arduino a través del L298N

Por las razones esgrimidas antes, la alimentación del Masaylo se producirá en base a las siguientes premisas:
- En ningún caso quitaremos el jumper del regulador.

Alimentación de Masaylo. Uso del L298N | 29
- Las tierras (polo negativo, GND) de Arduino y L298N deben estar interconectadas entre sí.
- Alimentaremos el L298 N desde el portapilas, y a nuestra Arduino desde el borne +5V del L298 N
En suma, el diagrama básico de conexión portapilas→L298n→Arduino y los motores DC quedaría así:

En el siguiente capítulo iniciaremos al lector en el movimiento simple (control todo-nada) del Masaylo mediante funciones sencillas.

Conexionado de los motores DC

### 30 Movimiento básico del Masaylo

# Movimiento básico del Masaylo

## Consideraciones iniciales

Ya se ha insistido varias veces en que los ejemplos contemplados en este libro están adaptados al pinout exhibido en el apartado correspondiente, y que es posible que alguno o ambos motores funcionen inversamente a lo esperado. En este caso, la solución es tan simple como intercambiar, en el L298N, sus correspondientes conexiones INx o OUTx, a gusto del lector.
Debe tenerse en cuenta también que ambos motores DC se encuentran en posición enfrentada, por lo que si queremos, por ejemplo, que el robot vaya hacia adelante, el motor izquierdo girará en sentido antihorario (visto desde enfrente de la rueda), y el derecho en sentido inverso. En el diagrama de conexiones proporcionado en este libro ya se ha tenido en cuenta, lo que no es óbice para que se pueda haber cometido algún error fácilmente solucionable por el lector mediante el intercambio de patillas explicado.

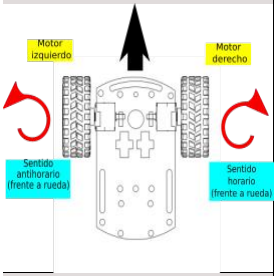
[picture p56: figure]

Mi primer programa: mover a Masaylo hacia adelante.

Recapitulemos: el motor izquierdo está asociado a las patillas 5 y 6 de nuestra Arduino, y el derecho a las 9 y 10. Visto así, y con la previsión de que ambos motores deben tener sus sentidos intercambiados, sólo tenemos que escribir un “1” lógico en las patillas 5 y 9 y un “0” en las patillas 6 y 10.
Empecemos por un ejemplo muy sencillo: hagamos que en setup(), Masaylo se mueva hacia adelante cinco segundos, para a continuación pararse:

Los movimientos rectos exigen sentidos de giro inversos

Movimiento básico del Masaylo | 31

Para detener un motor, bastará con poner a “0” o a “1” ambas patillas. Nosotros hemos optado por la segunda solución.

## Uso de funciones

Para agilizar la programación, y presuponiendo que el estudiante ya tiene cierto conocimiento del entorno de programación de Arduino, basado en C++, crearemos cinco funciones básicas de control del motor:

Mi primer programa con Masaylo: adelante y paro

void setup() {
//Designamos los pines correspondientes como salidas pinMode(5,OUTPUT);
pinMode(6,OUTPUT);
pinMode(9,OUTPUT);
pinMode(10,OUTPUT);
//Ponemos "1" y "0" según corresponda digitalWrite(5,HIGH);
digitalWrite(6,LOW);
digitalWrite(9,HIGH);
digitalWrite(10,LOW);
//Esperamos un tiempo
delay(5000);
//Ponemos un "1" en las dos patillas a nivel bajo digitalWrite(6,HIGH);
digitalWrite(10,HIGH);

}

void loop() {
//No queremos funcionamiento en bucle }

### 32 Movimiento básico del Masaylo

adelante()

Código | Movimiento
void adelante(){ digitalWrite(5,HIGH); digitalWrite(6,LOW); digitalWrite(9,HIGH); digitalWrite(10,LOW); }

atras()

Código | Movimiento
void atras(){ digitalWrite(5,LOW); digitalWrite(6,HIGH); digitalWrite(9,LOW); digitalWrite(10,HIGH); }

Movimiento básico del Masaylo | 33

izquierda()

Código | Movimiento
void izquierda(){ digitalWrite(5,LOW); digitalWrite(6,LOW); digitalWrite(9,LOW); digitalWrite(10,HIGH); }

derecha()

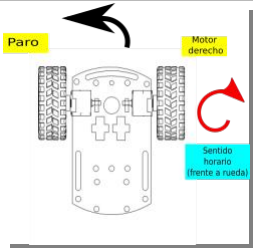
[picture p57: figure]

Código | Movimiento
void derecha(){ digitalWrite(5,HIGH); digitalWrite(6,LOW); digitalWrite(9,LOW); digitalWrite(10,LOW); }

### 34 Movimiento básico del Masaylo

alto()

Código | Movimiento
void alto(){ digitalWrite(5,LOW); digitalWrite(6,LOW); digitalWrite(9,LOW); digitalWrite(10,LOW); }

Programando Masaylo con funciones: izquierda, adelante,

## derecha,adelante, atras

El siguiente programa pretende proporcionar la base más simple posible al no iniciado para que comprenda el uso de funciones en programación: vamos a proporcionar a Arduino una secuencia de movimientos izquierda→adelante→derecha→adelante→alto→atras, de duración aleatoria entre 0,5 y 2 segundos cada movimiento.

Para facilitar el cambio de conexiones entre pines, a su vez, nos valdremos de la instrucción #DEFINE para utilizar referencias a los pines en lugar de escribir directamente los números.

//Asignamos una referencia a cada pin
#define MIA 5

#define MIB 6

#define MDA 9

#define MDB 10

//FUNCIONES DE MOVIMIENTO

void adelante (){

Movimiento básico del Masaylo | 35

digitalWrite(MIA,HIGH);
digitalWrite(MIB,LOW);
digitalWrite(MDA,HIGH);
digitalWrite(MDB,LOW);
}

void izquierda (){
digitalWrite(MIA,LOW);
digitalWrite(MIB,LOW);
digitalWrite(MDA,HIGH);
digitalWrite(MDB,LOW);
}

void derecha(){
digitalWrite(MIA,HIGH);
digitalWrite(MIB,LOW);
digitalWrite(MDA,LOW);
digitalWrite(MDB,LOW);
}

void atras(){
digitalWrite(MIA,LOW);
digitalWrite(MIB,HIGH);
digitalWrite(MDA,LOW);
digitalWrite(MDB,HIGH);
}
void alto(){
digitalWrite(MIA,LOW);
digitalWrite(MIB,LOW);

### 36 Movimiento básico del Masaylo

digitalWrite(MDA,LOW);
digitalWrite(MDB,LOW);
}

void setup() {
//Declaramos todos los pines como salidas digitales pinMode(MIA,OUTPUT);
pinMode(MIB,OUTPUT);
pinMode(MDA,OUTPUT);
pinMode(MDB,OUTPUT);
}
void loop() {
//Se llama a cada función en el orden deseado y duración especificada izquierda();
delay((int)random(500,2000));
adelante();
delay((int)random(500,2000)); derecha();
delay((int)random(500,2000)); adelante();
delay((int)random(500,2000)); alto();
delay((int)random(500,2000)); atras();
delay((int)random(500,2000)); }

Control de velocidad mediante PWM | 37

# Control de velocidad mediante PWM

## Regulación de velocidad en corriente continua

Como sabrán ya aquellos lectores con una cierta experiencia en el trabajo con tarjetas microcontroladoras como Arduino, no suele ser habitual la posibilidad de reproducir en estos dispositivos señales de tipo analógico, pero sí que es posible EMULAR dichas señales mediante la técnica denominada Pulse Width Modulation, o modulación por ancho de pulso, que en Arduino se resume en el uso de la función analogWrite(pin,velocidad).
A grandes rasgos, dicha técnica consiste en emitir “1” y “0” lógicos a través de la patilla elegida, alternándolos con una cierta frecuencia (pulsos), y cuya respectiva duración con respecto a la señal contraria supondrá un peso específico que marcará una media a lo largo del tiempo que oscilará entre 0 y 5 V.
Por ejemplo, si a lo largo de un segundo, alternamos 25 ciclos de 20 milisegundos con un “0” lógico (0 V en el pin) con otros 25 ciclos de igual duración pero con un “1” (5 V), el valor medio de dicha señal a lo largo de un segundo será exactamente de la mitad (2,5 V).
Si repartimos de manera distinta la duración de dichos pulsos, por ejemplo, 25 ciclos de 10 milisegundos para el “0”, alternándolos con con 25 ciclos de 30 milisegundos para el “1”, puede calcularse que el valor medio “emulado” (si seguimos trabajando con valores de 0 V y 5 V) es de 3,75 V.

## Uso de la función analogWrite(pin,velocidad)

Como ya se ha explicado, y sabrá el lector algo más avezado en Robótica Educativa, la tarjeta Arduino puede utilizar la técnica PWM en muchas de sus patillas mediante la función analogWrite(pin,velocidad). En la tarjeta Nano, concretamente, dicha función está disponible en los pines 3,5,6,9,10 y 11.
La función analogWrite() es muy fácil de utilizar . Sólo precisa de dos paŕametros entre paréntesis, separados por una coma, a saber: el pin en que queremos el pulso, y el valor que queremos establecer, válido entre 0 y 255. Así, 0, por ejemplo supondría 0 V, 127 emularía un valor de 2,5 V y 255 el valor completo de 5 V.

## Influencia del L298N sobre nuestra función analogWrite

Ya hemos explicado que el L298N es un circuito de transistores montados como puente en H que emiten a la salida una señal equivalente a la de la alimentación, con una cierta caída de tensión de algo más de 1 V (hasta 1,5 V) en ocasiones. Si alimentamos el Masaylo con tensiones inferiores a los 6 V que dará nuestro portapilas, podemos encontrarnos con errores en el funcionamiento del robot usando esta técnica que redunden incluso en su imposibilidad de moverse. Si alimentáramos, por el contrario, al robot con tensiones superiores, por ejemplo, 9 V, habrá variaciones en su

### 38 Control de velocidad mediante PWM

comportamiento que permitirán un control más afinado de las velocidades, pero ello obligará a su vez al programador a estar pendiente de no sobrepasar valores que supongan tensiones perjudiciales para el motor DC (no aconsejamos superar los 6 V en bornes), si bien son elementos muy estables y sólidos (por eso aguantan tantos años en talleres de Tecnología en Educación Secundaria).

## Uso de funciones para control de velocidad en el Masaylo

En el capítulo anterior, utilizábamos la función digitalWrite(pin,estado) en las patillas que controlaban cada motor en sus bornes escribiendo “1” (5V) y “0” (0V) en cada una de las patillas. Para regular la velocidad, seguiremos utilizando digitalWrite() para escribir “0” en uno de los contactos del motor, por un lado, y analogWrite(), por otro, para establecer un pulso que a lo largo del tiempo produzca el efecto de la señal que queremos en dicho contacto.
Hay que tener claro, por otro lado, que estos motores DC necesitan un valor mínimo de entre 3 y 3,5 V para empezar a moverse,. Por ello, aunque el valor máximo de analogWrite es 255, (equivalente,

Fuente: Wikimedia Commons. Distribución de los ciclos de trabajo en PWM usando analogWrite()

Control de velocidad mediante PWM | 39

en un principio, a 5 V), el valor mínimo no debería bajar de un número dictado por la experiencia en cada robot, y que para nosotros no debería bajar de 120.
Igual que hemos hecho en el capítulo anterior, proponemos una serie de funciones que simplifiquen la programación del robot en orden a disponer movimientos controlados.

adelante(valor)

Código | Movimiento
void adelante(int valor){ analogWrite(5,valor); digitalWrite(6,LOW); analogWrite(9,valor); digitalWrite(10,LOW); }

atras(valor)

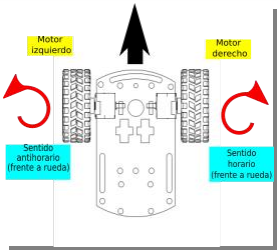
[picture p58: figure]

Código | Movimiento
void atras(int valor){ digitalWrite(5,LOW); analogWrite(6,valor); digitalWrite(9,LOW); analogWrite(10,valor); }

### 40 Control de velocidad mediante PWM

izquierda(valor)

Código | Movimiento
void izquierda(int valor){ digitalWrite(5,LOW); digitalWrite(6,LOW); digitalWrite(9,LOW); analogWrite(10,valor); }

derecha(valor)

Código | Movimiento
void derecha(int valor){ analogWrite(5,valor); digitalWrite(6,LOW); digitalWrite(9,LOW); digitalWrite(10,LOW); }

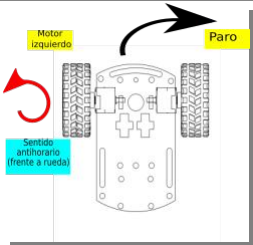
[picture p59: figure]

No debe preocupar al lector la coincidencia en los nombres de dichas funciones con las del capítulo anterior; ambos tipos pueden convivir en el mismo programa de Arduino gracias a lo que se conoce en programación como SOBRECARGA DE FUNCIONES
La función alto(), definida en el capítulo anterior, sigue siendo lógicamente válida dado que no es posible modular la velocidad en un vehículo parado.

Control de velocidad mediante PWM | 41

## Ejemplo de control de velocidad de Masaylo mediante funciones y PWM

El siguiente programa establece tres valores de velocidad discretos elegidos a voluntad como lento, ligero y rápido, asociados a los valores enteros 140, 200 y 255. Estableceremos una única secuencia de movimiento, por ejemplo, adelante rápido→ adelante ligero→adelante lento→ derecha lenta→ atrás lenta→ atrás media→izquierda rápida, separadas por intervalos de dos segundos para movimientos rectos y medio segundo para los giros. Veamos pues:
//Asignamos una referencia a cada pin
#define MIA 5

#define MIB 6

#define MDA 9

#define MDB 10

//FUNCIONES DE MOVIMIENTO DE VELOCIDAD REGULADA void adelante(int valor){
analogWrite(5,valor);
digitalWrite(6,LOW);
analogWrite(9,valor);
digitalWrite(10,LOW);
}

void atras(int valor){
digitalWrite(5,LOW);
analogWrite(6,valor);
digitalWrite(9,LOW);
analogWrite(10,valor);
}
void izquierda(int valor){ digitalWrite(5,LOW);
digitalWrite(6,LOW);
digitalWrite(9,LOW);
analogWrite(10,valor);
}
void derecha(int valor){
analogWrite(5,valor);
digitalWrite(6,LOW);
digitalWrite(9,LOW);
digitalWrite(10,LOW);
}
void alto(){
digitalWrite(5,LOW);
digitalWrite(6,LOW);

### 42 Control de velocidad mediante PWM

digitalWrite(9,LOW);
digitalWrite(10,LOW);
}
void setup() {
//Declaramos todos los pines como salidas digitales pinMode(MIA,OUTPUT);
pinMode(MIB,OUTPUT);
pinMode(MDA,OUTPUT);
pinMode(MDB,OUTPUT);
//Se llama a cada función en el orden deseado y duración especificada //adelante rápido, ligero y lento
adelante(255);
delay(2000);
adelante(200);
delay(2000);
adelante(150);
delay(2000);
//derecha lenta
derecha(150);
delay(500);
//atrás lenta y media
atras(150);
delay(2000);
atras(200);
delay(2000);
//izquierda rápida
izquierda(255);
delay(500);
//Paramos
alto();

Control de velocidad mediante PWM | 43

}

void loop() {
//No trabajamos en bucle en este ejemplo }

### 44 Trabajo con sensores: detección de distancias con el HC-SR04

# Trabajo con sensores: detección de distancias con el HC-SR04

## Detección de distancias por ultrasonidos

Como casi todos los otros campos de conocimientos tratados a lo largo de este texto relacionados con la Robótica Educativa, existe ya una extensa bibliografía en la red sobre el uso de módulos como el HC-SR04 o el PING de Parallax en la red. No queremos dejar pasar la ocasión de llamar la atención del lector con respecto a un genial artículo del ya mencionado Luis Llamas. (https://www.luisllamas.es/medir-distancia-con-arduino-y-sensor-de-ultrasonidos-hc-sr04/)
El principio básico de cualquier sensor de ultrasonidos es muy sencillo:
- Un circuito emisor, comúnmente denominado “Trigger”, lanza un pulso de ultrasonidos (para ello, Arduino debe emitir un “1” en la patilla correspondiente).
- Un temporizador se pone a 0 y empieza a contar.
- Un circuito receptor, de nombre común “Echo”, detecta el ultrasonido que ha rebotado (siempre que haya obstáculo) y envía un “1” lógico a una patilla de Arduino (puede ser o no la misma que hemos conectado al emisor, dependiendo del modelo).
- Detectado el “1” lógico en el pin conectado a “Echo” el temporizador se para.

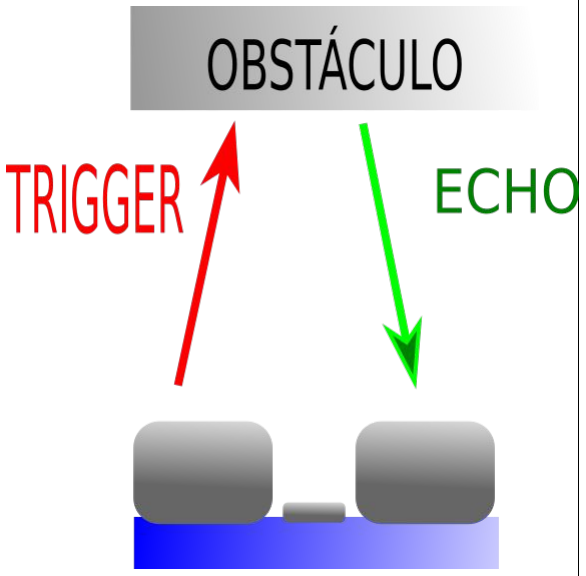
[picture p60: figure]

Principio de funcionamiento del sensor de ultrasonidos

Trabajo con sensores: detección de distancias con el HC-SR04 | 45
- Conocida la velocidad del sonido (unos 343 m/sg), y que el sonido ha tenido que recorrer el espacio hasta el obstáculo dos veces, ida y vuelta, se realiza el cálculo correspondiente. En recorrer 1 cm, el tiempo que tarda el sonido es 0,000029155 sg. Teniendo en cuenta que la distancia es doble, un obstáculo localizado a 1 cm del sensor tardaría en detectarse 0,000058309 sg, es decir, 58,309 microsegundos, valor que utilizaremos para convertir el tiempo medido en distancia en cm.

## Función básica para leer distancias con el HC-SR04

Ya indicamos en capítulos anteriores los pines que hemos previsto para el sensor de ultrasonidos: 7 para Trigger (habrá que declararlo como OUTPUT), y 8 para Echo (INPUT), tal como puede verse en la imagen. Como ocurre con todos los sensores de esta naturaleza, hay también siempre una patilla para conectar a +5 V (alimentación) y otra a tierra (GND).

A la función que utilizaremos para aprender a utilizar este sensor la llamaremos dameDistancia(), que devolverá un valor de tipo long:

long dameDistancia(){
long espacio;
long tiempo;
//Apagamos (para evitar falsas lecturas) y encendemos Trigger durante 10 us digitalWrite(_7,LOW);

Trigger va al pin 7, Echo al 8.

### 46 Trabajo con sensores: detección de distancias con el HC-SR04

delayMicroseconds(4);
digitalWrite(8,HIGH);
delayMicroseconds(10);
digitalWrite(7,LOW);
//Medimos el tiempo en us que tarda en volver el pulso y realizamos el cálculo. tiempo=pulseIn(8,HIGH);
espacio=tiempo/58.309;
//La función devuelve un valor de tipo long correspondiente a la distancia en cm. return espacio;
}

## Ejemplo 1: detección de distancias y comunicación vía puerto

serie.

El presente programa utiliza la función dameDistancia() para medir el espacio entre el sensor y un obstáculo delante del Masaylo para pasarlo a continuación por el puerto serie:
//Definimos los pines echo y trigger
#define trig 7

#define echo 8

long dameDistancia(){
long espacio;
long tiempo;
//Apagamos (para evitar falsas lecturas) y encendemos Trigger durante 10 us digitalWrite(trig,LOW);
delayMicroseconds(4);
digitalWrite(trig,HIGH);
delayMicroseconds(10);
digitalWrite(trig,LOW);
//Medimos el tiempo en us que tarda en volver el pulso y realizamos el cálculo. tiempo=pulseIn(echo,HIGH);
espacio=tiempo/58.309;

Trabajo con sensores: detección de distancias con el HC-SR04 | 47

//La función devuelve un valor de tipo long correspondiente a la distancia en cm. return espacio;
}
void setup() {
//trigger es OUTPUT, echo INPUT pinMode(trig, OUTPUT);
pinMode(echo,INPUT);
//Inicializamos el puerto serie Serial.begin(9600);
}

void loop() {
//Utilizamos una variable local
long distancia=dameDistancia(); //Imprimimos la variable por el puerto serie Serial.print("Distancia: "); Serial.println(distancia);
//Tiempo mínimo para evitar desfases delay(100);
}

## Ejemplo 2: Masaylo salvaobstáculos

Apliquemos lo aprendido para que Masaylo se mueva libremente hacia adelante salvo que se encuentre un obstáculo entre 40 y 20 cm de distancia, en cuyo caso reducirá la marcha. Si el obstáculo se encuentra a menos de 20 cm, se irá hacia atrás y girará hacia la derecha para buscar otro camino.
//Asignamos una referencia a cada pin
#define MIA 5

#define MIB 6

#define MDA 9

### 48 Trabajo con sensores: detección de distancias con el HC-SR04

#define MDB 10

#define trig 7

#define echo 8

//FUNCIÓN DE MEDICIÓN DE DISTANCIA long dameDistancia(){
long espacio;
long tiempo;
//Apagamos (para evitar falsas lecturas) y encendemos Trigger durante 10 us digitalWrite(trig,LOW);
delayMicroseconds(4);
digitalWrite(trig,HIGH);
delayMicroseconds(10);
digitalWrite(trig,LOW);
//Medimos el tiempo en us que tarda en volver el pulso y realizamos el cálculo. tiempo=pulseIn(echo,HIGH);
espacio=tiempo/58.309;
//La función devuelve un valor de tipo long correspondiente a la distancia en cm. return espacio;
}
//FUNCIONES DE MOVIMIENTO

void adelante (){
digitalWrite(MIA,HIGH);
digitalWrite(MIB,LOW);
digitalWrite(MDA,HIGH);
digitalWrite(MDB,LOW);
}

void izquierda (){

Trabajo con sensores: detección de distancias con el HC-SR04 | 49

digitalWrite(MIA,LOW);
digitalWrite(MIB,LOW);
digitalWrite(MDA,HIGH);
digitalWrite(MDB,LOW);
}

void derecha(){
digitalWrite(MIA,HIGH);
digitalWrite(MIB,LOW);
digitalWrite(MDA,LOW);
digitalWrite(MDB,LOW);
}

void atras(){
digitalWrite(MIA,LOW);
digitalWrite(MIB,HIGH);
digitalWrite(MDA,LOW);
digitalWrite(MDB,HIGH);
}
void alto(){
digitalWrite(MIA,LOW);
digitalWrite(MIB,LOW);
digitalWrite(MDA,LOW);
digitalWrite(MDB,LOW);
}

//FUNCIONES DE MOVIMIENTO DE VELOCIDAD REGULADA void adelante(int valor){
analogWrite(MIA,valor);
digitalWrite(MIB,LOW);
analogWrite(MDA,valor);

### 50 Trabajo con sensores: detección de distancias con el HC-SR04

digitalWrite(MDB,LOW);
}

void atras(int valor){
digitalWrite(MIA,LOW);
analogWrite(MIB,valor);
digitalWrite(MDA,LOW);
analogWrite(MDB,valor);
}
void izquierda(int valor){ digitalWrite(MIA,LOW);
digitalWrite(MIB,LOW);
digitalWrite(MDA,LOW);
analogWrite(MDB,valor);
}
void derecha(int valor){
analogWrite(MIA,valor);
digitalWrite(MIB,LOW);
digitalWrite(MDA,LOW);
digitalWrite(MDB,LOW);
}

void setup() {
//Declaramos cada pin en el modo en que corresponda pinMode(trig,OUTPUT);
pinMode(echo,INPUT);
pinMode(MIA,OUTPUT);
pinMode(MIB,OUTPUT);
pinMode(MDA,OUTPUT);
pinMode(MDB,OUTPUT);
}
void loop() {
//Medimos la distancia y la asignamos a una variable local long distancia=dameDistancia();
if (distancia>30){
//No hay obstáculos a la vista adelante();

Trabajo con sensores: detección de distancias con el HC-SR04 | 51

}else if (distancia<20){
//Obstáculo ineludible, paro, atrás y derecha alto();
delay(500);
atras();
delay(2000);
derecha();
delay(500);
}else{
//Obstáculo entre 20 y 30 cm. Proceder con cautela adelante(150);
}
//Damos tiempo para evitar problemas de desfases delay(100);
}

### 52 Trabajo con sensores: siguelíneas con sensores de infrarrojos

# Trabajo con sensores: siguelíneas con sensores de infrarrojos

## Características de los sensores de infrarrojos

Un sensor de infrarrojos participa del mismo principio funcional que uno de ultrasonidos: se alimenta un diodo LED infrarrojo para que emita un pulso de luz,detectable por un fototransistor, en caso de haber rebotado en algún obstáculo. No obstante, este tipo de sensores presenta características propias que lo distingue de un sensor de ultrasonidos:
Ventajas
- Son sensiblemente más baratos
- Disponen de un potenciómetro que permite ajustar la sensibilidad del sensor
- La emisión de la luz infrarroja es continua, no se necesita pin de control. Así que sólo hacen falta tres conexiones: V, GND y OUT (pin de señal). Son más fáciles de instalar y de manejo más simple por parte del sistema de control.
- Pueden detectar cambios, si no de color, sí de luminosidad en la superficie sobre la que apuntan, lo que les hace ideales para el diseño de robot siguelíneas.
Desventajas
- Su rango de detección es sensiblemente más bajo que en el caso de los ultrasonidos. Raramente superan los 30 cm, en el mejor de los casos, en el FC-51, y menos de 20 mm en el TCRT5000
- Su sensibilidad es muy vulnerable a los cambios de luz en la estancia en la que se encuentre el robot, lo que obliga a continuos reajustes mediante el potenciómetro anexo. En ocasiones es recomendable rodear el par formado por el LED y el fototransistor por algún tipo de capuchón improvisado con cinta o cartón que reduzca al máximo el ruido ocasionado por dichos cambios de luz.

## Conexionado y lectura de sensores infrarrojos

Masaylo incorpora soportes para dos tipos de sensores: el FC-51 y el TCRT5000. En estas líneas desarrollaremos el trabajo con el FC-51, que es el que teníamos a mano en el momento de redactarlas. El conexionado y proceso de lectura en ambos casos son los mismos. La diferencia entre ambos estriba en que tenemos la sensación de que el TCRT5000 puede ser más eficaz en el caso del siguelíneas, mientras que los FC-51 podrían ser más útiles si queremos hacerlos servir como sensores secundarios al de ultrasonidos en el caso del salvaobstáculos.

Trabajo con sensores: siguelíneas con sensores de infrarrojos | 53

Este tipo de sensor, como ya se ha dicho, tiene tres patillas: dos de alimentación (5V y GND) y la de señal (OUT). En nuestro planteamiento de pinout, hemos establecido el patillaje:
- Sensor de infrarrojos izquierdo→ Pin 2 de Arduino
- Sensor de infrarrojos derecho→ Pin 3 de Arduino

Dado que son señales que Arduino debe leer, ambos pines (o los que elija el estudiante) deben ser puestos en modo INPUT.
El comportamiento de estos sensores sigue las siguientes pautas:
- Si la luz rebota en el fototransistor, significa que hay obstáculo o que se está detectando un color claro (se lee “blanco”). En la patilla OUT se leerá un “0” lógico
- Si la luz no vuelve al sensor, se entiende que no hay obstáculo, o que sí lo hay pero su superficie es lo bastante oscura como para absorberla (se lee “negro”). En la patilla OUT se leerá un “1” lógico.

## Programación de Masaylo como siguelíneas

Un clásico en robótica educativa es la programación de un siguelíneas. La idea es conseguir un sistema autónomo capaz de seguir un camino que tenga un tono claramente distinto de su entorno, normalmente una línea negra sobre fondo blanco. Para ello, existen múltiples métodos y de muy

Los sensores de infrarrojos izquierdo y derecho se conectan a los pines 2 y 3.

### 54 Trabajo con sensores: siguelíneas con sensores de infrarrojos

diversa complejidad. En los robots de carreras se utiliza el cálculo PID (Proporcional-Integrativo-Derivativo), normalmente con muchos más de dos sensores. El uso, por otro lado, de motores de tipo paso a paso permite un control del movimiento muy necesario en este tipo de trabajos, aunque ello redunde, al menos en el caso de los modelos menos caros, en una clara pérdida de la velocidad. Como Masaylo es un robot de muy bajo coste, pensado principalmente para la introducción del estudiante a los principios más básicos de este campo, optaremos por una solución intermedia que exigirá, eso sí, un riguroso calibrado de los sensores (potenciómetro mediante) antes de cada prueba práctica. Por otro lado, recalcar que no es conveniente utilizar funciones de movimiento de tipo todo/nada en este caso, dado que un motor DC proporciona excesiva potencia para dar tiempo al robot a reaccionar a los cambios en la trayectoria. Optaremos, en cambio, por el uso de
movimientos de velocidad regulada mediante la función analogWrite() que comentábamos hace tres capítulos.
La idea es la siguiente: mientras ambos sensores envíen un “0” lógico al sistema de control, significa que nuestro vehículo sigue correctamente el camino, y enviaremos la orden de “adelante” a una velocidad adecuada (depende de la experiencia con cada robot). En cambio, si el sensor derecho, por ejemplo, envía un “1” (pisamos el camino por la derecha), significa que nos estaremos saliendo por la izquierda, así que habrá que girar hacia la derecha para compensar nuestra trayectoria. Lo mismo sucederá si el sensor izquierdo envía un “1” (nos salimos por la izquierda, hay que girar hacia la derecha).

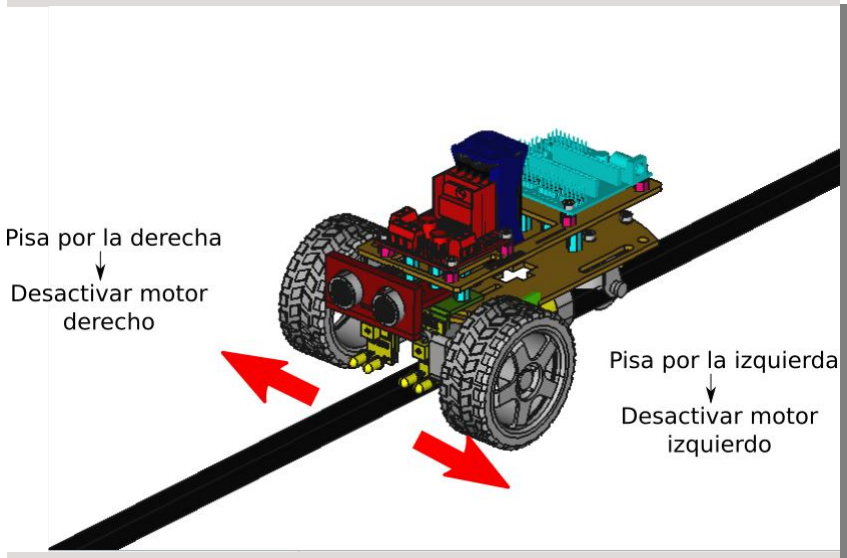
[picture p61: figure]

¿Y qué sucederá si ambos sensores envían un “1” lógico?. Sucederá que, por algún error, el vehículo está mirando perpendicularmente a una parte del camino. El programador puede idear varias estrategias para que el robot retroceda y trate de retomar su camino. Por razones de simplicidad (es nuestro primer siguelíneas), nosotros lo pararemos.

Funcionamiento de un robot siguelíneas

Trabajo con sensores: siguelíneas con sensores de infrarrojos | 55

Para simplificar la programación, hemos diseñado que llamaremos leeSuelo() y que devuelve un valor de tipo int, en base al cual decidiremos la estrategia a seguir: 0→adelante, 1→derecha,2→izquierda, 3→ alto.
//Recuerde el lector adaptar el programa a su propia elección de pines.
#define sIzquierda 2

#define sDerecha 3

int leeSuelo(){ //Los sensores dan 1 para negro, 0 para blanco

int valor=0; if (digitalRead(sDerecha)==HIGH){ valor=valor+1; } if (digitalRead(sIzquierda)== valor=valor+2; } return valor; }

## Planteamiento: programar a Masaylo como siguelíneas

A continuación, aglutinando todo lo explicado hasta ahora en este libro, presentamos un programa de control de la velocidad en los motores DC de nuestro robot de acuerdo a la información enviada por los sensores infrarrojos. Como decíamos antes, la velocidad elegida (de valores que oscilarían entre 120 y 255) en cada motor dependerá de las propias circunstancias de cada robot en cada caso, previa calibración de dichos sensores. Nuestra elección ha sido de 130 para adelante() y de 150 para izquierda() y derecha(), aunque el estudiante puede experimentar con valores distintos.
//Definimos patillaje #define MIA 5 #define MIB 6 #define MDA 9 #define MDB 10 #define sDerecha 3 #define sIzquierda 2

//Declaramos la variable global valorLeido que recogerá la lectura de los sensores int valorLeido;
//Escribimos las funciones de movimiento de velocidad controlada

### 56 Trabajo con sensores: siguelíneas con sensores de infrarrojos

void alto(){ digitalWrite(MIA,LOW);

digitalWrite(MIB,LOW); digitalWrite(MDA,LOW);

digitalWrite(MDB,LOW); }

void adelante( int velocidad){ analogWrite(MIA,velocidad); digitalWrite(MIB,LOW); analogWrite(MDA,velocidad); digitalWrite(MDB,LOW); }

void izquierda(int velocidad){ digitalWrite(MIA,LOW);
digitalWrite(MIB,LOW);
analogWrite(MDA,velocidad); digitalWrite(MDB,LOW);
}

void derecha(int velocidad){ analogWrite(MIA,velocidad); digitalWrite(MIB,LOW);
digitalWrite(MDA,LOW);
digitalWrite(MDB,LOW);
}
//No la utilizamos en este caso, pero puede ser útil para modificaciones posteriores void atras(int velocidad){
analogWrite(MIB,velocidad);
digitalWrite(MIA,LOW);
analogWrite(MDB,velocidad); digitalWrite(MDA,LOW);
}
//Función de lectura de sensores siguelíneas leeSuelo()
int leeSuelo(){
//Los sensores dan 1 para negro, 0 para blanco. Valor recoge el total de las lecturas int valor=0;

Trabajo con sensores: siguelíneas con sensores de infrarrojos | 57

//Si pisamos por la derecha, sumamos 1 if (digitalRead(sDerecha)==HIGH){ valor=valor+1; }

//Si pisamos por la derecha, sumamos 2 if (digitalRead(sIzquierda)==HIGH){ valor=valor+2; } return valor; }

//Configuración
void setup() {
//Pines en modo lectura/escritura pinMode(MIA,OUTPUT);
pinMode(MIB,OUTPUT);
pinMode(MDA,OUTPUT);
pinMode(MDB,OUTPUT);
pinMode(sDerecha, INPUT);
pinMode(sIzquierda, INPUT); valorLeido=0;
}
//Masaylo empieza su singladura
void loop() {
//Llamamos a la función de lectura de los sensores valorLeido=leeSuelo();
//Decidimos según lectura
switch(valorLeido){
case 3:
alto();
break;
case 1:
derecha(150);
break;
case 2:
izquierda(150);
break;
case 0:
adelante(130);

### 58 Trabajo con sensores: siguelíneas con sensores de infrarrojos

break; }

}

Comunicación inalámbrica a través del módulo Bluetooth. | 59

# Comunicación inalámbrica a través del

módulo Bluetooth.

## Principios básicos

Pasamos en este capítulo a uno de los aspectos de la Robótica Educativa que a los autores más nos ha apasionado a lo largo de los últimos años, y al mismo tiempo, más pereza nos da abordar en este humilde texto, por lo variado y multidisciplinar de los principios que hay que abordar para dotar al lector de un conocimiento suficiente para comunicarse con el Masaylo inalámbricamente. La comunicación vía Bluetooth.
Existen múltiples módulos para proporcionar este tipo de comunicación con Arduino. Dado que son los más populares, trabajaremos con el modelo HC-05 ó el HC-06. La diferencia de precio entre ambos modelos es mínima, y si bien el HC-05 nos ofrece la oportunidad de trabajar como maestro o como esclavo, mientras que su antagonista sólo ofrece esta última opción, a efectos prácticos nos será indiferente trabajar con uno u otro modelo en nuestro Masaylo. El HC-05 tiene seis pines, de los cuales sólo trabajaremos con los cuatro que tiene en común con el HC-06:
- VCC (alimentación a 5 V)
- GND (tierra)
- Tx (transmisión)
- Rx (Recepción) (CUIDADO: algunos módulos BT más antiguos sólo admiten tensiones de 3.3 V, lo cual puede aconsejar conectar este pin a Arduino, que da +5 V en los “1” lógicos, a través de un divisor de tensión. Consúltese la documentación correspondiente al módulo adquirido).
En el HC-05 existen otros dos pines, EN y STATE. No los conectaremos.
Excede en mucho el propósito de este libro entrar en más detalle sobre ello, pero conviene también reseñar que para aprovechar este capítulo, el estudiante debería tener ya un cierto conocimiento sobre un aspecto del trabajo con Arduino que no se ha tratado aún en este texto: la comunicación con el microcontrolador vía puerto serie.
El puerto serie (emulado) es el medio que normalmente utiliza Arduino para comunicar el microcontrolador con el ordenador con el objetivo de volcar nuestro programa en memoria. Para ello, utiliza los pines 0 (Rx) y 1 (Tx) de la tarjeta para leer y escribir información, respectivamente. Es por ello por lo que normalmente se desaconseja el uso de ambos pines para conectar sensores o actuadores, salvo como último recurso, dado que entonces nos privaremos de la posibilidad de grabar nuevos programas o comunicarnos con la tarjeta a través del ordenador.
Es por ello que, en nuestro caso, utilizaremos una librería que normalmente viene instalada por defecto en el IDE de Arduino (y si no, puede instalarse fácilmente), llamada SoftwareSerial, y que

60 Comunicación inalámbrica a través del módulo Bluetooth.

nos permite emular esta comunicación por software en lugar del hardware de los mencionados pines, utilizando, en su lugar, las patillas 12 y 13.

## Conexionado del módulo BT y velocidad de comunicación

El flujo de trabajo en el uso de módulos de comunicación obedece a tres enfoques:
- Cada módulo (como el resto del hardware presente en el robot) debe tener una alimentación adecuada que proporcione suficiente intensidad de corriente y se mantenga en el rango de tensiones adecuada. Como decíamos, la mayoría de los módulos Bluetooth en el mercado de hoy están preparados para trabajar con 5 V, aunque su tensión de trabajo sea de 3.3. V, gracias a la presencia de reguladores de tensión. No obstante, es posible aún encontrar algún modelo antiguo que necesite, al menos en la patilla Rx, un divisor de tensión que evite daños al módulo.
- La patilla Rx (recepción) del módulo BT se conectará a la Tx (transmisión) de la Arduino, y viceversa.
- Es importante SABER A QUÉ VELOCIDAD DE COMUNICACIÓN TRABAJA EL MÓDULO QUE HEMOS INSTALADO. Las velocidades más comunes son 9600 ó 19200 baudios. LA VELOCIDAD POR DEFECTO EN LOS CÓDIGOS DE EJEMPLO SERÁ DE 19200 BAUDIOS, pero el lector modificará este parámetro de modo acorde a su propia situación.
En los módulos BT puede configurarse, no sólo su velocidad de comunicación, sino también su nombre, su rol como maestro/esclavo (en el caso del HC-05), amén de otras posibilidades. De nuevo, esta posibilidad excede con mucho la intención de este libro, y animamos al lector a que bucee en la extensa bibliografía que puede encontrar a este respecto en Internet.
Otro aspecto que puede ser más espinoso, o que al menos puede plantear varios ensayos de prueba y error, es la comunicación con el módulo BT mediante un dispositivo, normalmente un smartphone o una tablet. Será necesario utilizar una app que se comunique con el módulo vía consola de texto, y que dependiendo del sistema operativo utilizado, puede ser un modelo u otro. Dada la variedad de programas de este tipo que existen en el mercado, y todos de carácter más o menos comercial, nos perdonará el lector si no nos inclinamos por recomendar ninguno. La elección de dicha app queda a su libre albedrío.
La comunicación por el puerto serie vía inalámbrica puede resultar complicada, al menos las primeras veces. Recomendamos al lector que en sus primeros intentos aumente la simplicidad al máximo, teniendo en cuenta que:
- Es recomendable utilizar los elementos más sencillos posibles como comandos. Un carácter es mejor que una palabra entera, un número entero mejor que un carácter, y un byte mejor que un número.

Comunicación inalámbrica a través del módulo Bluetooth. | 61
- En la comunicación por puerto Serie, tanto en la app como en Arduino, hay que indicar no sólo la velocidad en baudios, sino cómo se señaliza cada línea nueva. La opción más común es Ambos NL&CR
El diagrama de conexionado del módulo BT, como todos los presentados en el manual, es muy sencillo. Como siempre, queda a disposición del estudiante elegir otros pines para su propio diseño, siempre que recuerde que el pin al que conecte Rx del módulo se entenderá como Tx en el programa en Arduino, y al revés (pues la tarjeta leerá la información envíada vía BT y enviará en su caso la información correspondiente).

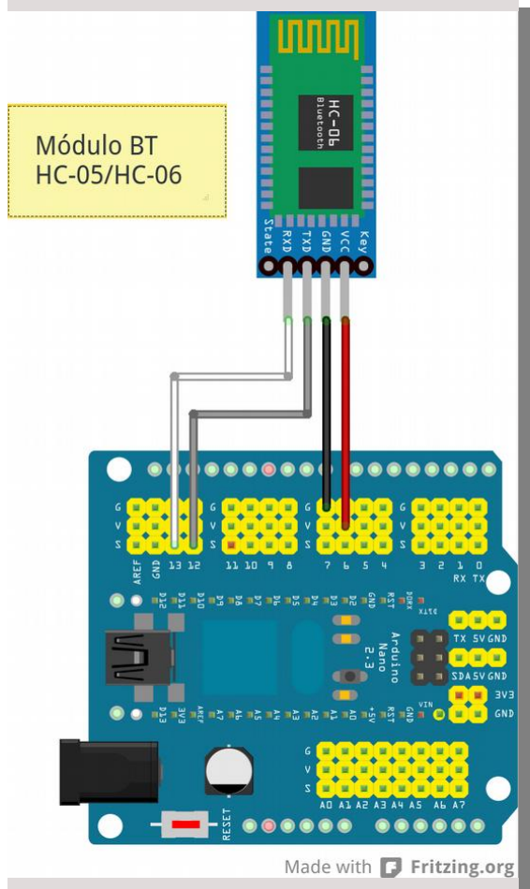
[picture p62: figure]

Comunicación de nuestro dispositivo con el módulo BT.

Como comentábamos hace unas líneas, uno de los momentos más complicados puede ser el de vincular el módulo BT con nuestro smartphone o tableta. Dependiendo del sistema operativo utilizado, hay que seguir unos pasos u otros, pero existen pautas comunes en todos los casos:
- Hay que activar el dispositivo Bluetooth de nuestro dispositivo (obvio).

En los códigos de
ejemplo, asignamos Tx al
pin 12 y Rx al 13

62 Comunicación inalámbrica a través del módulo Bluetooth.

- Buscar el módulo de BT para emparejarlo con nuestro dispositivo (por defecto, normalmente de nombre HC-05 ó HC-06; en el caso de la ilustración, hemos cambiado su nombre a través de comandos AT).
- El password de este tipo de módulos, por defecto, suele ser “1234”.

Comunicación inalámbrica a través del módulo Bluetooth. | 63

## Código base de control del Masaylo vía Bluetooth

El siguiente código utiliza la librería <SoftwareSerial.h> que suele venir por defecto en la IDE de Arduino para comunicarse con el módulo BT a través de los pines 12 y 13. Incluye varios aspectos tratados en capítulos anteriores, como el manejo de motores DC a través del L298N o el uso de funciones. Asumiendo que el estudiante tiene ya un cierto dominio del uso de puerto serie como vía de comunicaciones, el programa trabaja así:
- Emula un puerto serie vía software en los pines establecidos (el estudiante puede elegir otros), indicando mediante begin la velocidad (19200 baudios en nuestro ejemplo; dependiendo del modelo, quizás haya que cambiarlo a 9600 u otro valor).
- A cada comienzo del ciclo loop(), comprueba si hay información nueva en el puerto serie. De ser así, espera un carácter. Según éste sea ‘a’,‘r’, ‘i’, ‘d’ ó ‘p’, se llamará a las funciones de movimiento adelante(), atras(), izquierda(), derecha() o alto().
- Las funciones de movimiento todo-nada son las mismas utilizadas en anteriores ejemplos.
- Para enviar las órdenes, hay que tener instalada una app que se conecte con nuestro módulo BT y que emule una consola que pueda enviar información al módulo. El lector controlará a distancia a Masaylo enviando los caracteres correspondientes (téngase en cuenta, insistimos, la necesidad de tener controlado el modo de retorno de carro, normalmente de tipo Nueva línea&Retorno de carro).
//Incluimos la librería SoftwareSerial
#include<SoftwareSerial.h>

//Definimos el pinout
const byte rxPin = 12;
const byte txPin = 13;
#define MIA 5

#define MIB 6

#define MDA 9

#define MDB 10

//Declaramos un puerto serie emulado al que llamaremos miSerial en los pines especificados SoftwareSerial miSerial(rxPin, txPin);
void setup() {
// La velocidad del puerto serie debe ser acorde a la del módulo BT

64 Comunicación inalámbrica a través del módulo Bluetooth.

miSerial.begin(19200);
pinMode(MIA,OUTPUT);
pinMode(MIB,OUTPUT);
pinMode(MDA,OUTPUT);
pinMode(MDB,OUTPUT);
}

void loop() {
//Comprobamos si se ha recibido información nueva if (miSerial.available()>0){

valor=miSerial.read();

// Serial.println(valor);
if (valor=='a'){
adelante();
}
if (valor=='r'){
atras();
}
if (valor=='i'){
izquierda();
}
if (valor=='d'){
derecha();
}
if (valor=='p'){
alto();
}

Comunicación inalámbrica a través del módulo Bluetooth. | 65

}
}

void alto(){
digitalWrite(MIA,LOW);
digitalWrite(MIB,LOW);
digitalWrite(MDA,LOW);
digitalWrite(MDB,LOW);
}

void adelante(){
digitalWrite(MIA,HIGH);
digitalWrite(MIB,LOW);
digitalWrite(MDA,HIGH);
digitalWrite(MDB,LOW);
}

void izquierda(){
digitalWrite(MIA,LOW);
digitalWrite(MIB,LOW);
digitalWrite(MDA,HIGH);
digitalWrite(MDB,LOW);
}

void derecha(){
digitalWrite(MIA,HIGH);
digitalWrite(MIB,LOW);
digitalWrite(MDA,LOW);
digitalWrite(MDB,LOW);

66 Comunicación inalámbrica a través del módulo Bluetooth.

}

void atras(){
digitalWrite(MIB,HIGH);
digitalWrite(MIA,LOW);
digitalWrite(MDB,HIGH);
digitalWrite(MDA,LOW);
}

## Programando con AppInventor: MasayloBT.apk

En los repositorios en los que se encuentra este manual, dentro de la carpeta Code, hemos incluido un humilde software que lee los giróscopos de un smartphone o tablet y nos permite enviar los caracteres que controlan el Masaylo en el anterior programa. Así, sólo tendremos que inclinar el dispositivo hacia adelante, atrás, izquierda o derecha para controlarlo. El archivo se llama MasayloBT.apk y funciona en Android.
Su funcionamiento es sencillo. Una vez arrancado, pulsamos en el botón Conectar BT para buscar el nombre del módulo de Masaylo que previamente habremos emparejado con nuestro smartphone o tableta.

Se abrirá entonces una lista con los distintos dispositivos Bluetooth que a lo largo de la vida útil de nuestro dispositivo habremos utilizado:

Comunicación inalámbrica a través del módulo Bluetooth. | 67

Una vez elegido nuestro módulo, saldrá un mensaje indicando que todo ha ido bien. A partir de ahí, bastará con inclinar ligeramente en uno u otro sentido el teléfono para que el Masaylo se mueva en consonancia.

Sólo hay que pulsar en el botón Desconectar cuando hayamos acabado de jugar.

### 68 Uso de librerías

# Uso de librerías

## La librería Masaylo

Uno de los grandes atractivos que ofrece Arduino y su IDE es la posibilidad de utilizar librerías como herramientas para programar de un modo más sencillo, obteniendo resultados muchos más satisfactorios. Los autores no nos hemos sustraído a este atractivo, y hemos cedido a la tentación de implementar una librería propia para Masaylo con el mismo nombre, y que se encuentra a disposición del lector en los repositorios GIT, dentro de la carpeta libraries. En dicha carpeta se encuentra el archivo Masaylo.zip, que puede instalarse en nuestra IDE siguiendo el método habitual, esto es, Programa→ Incluir Librería→ Añadir librería .ZIP…

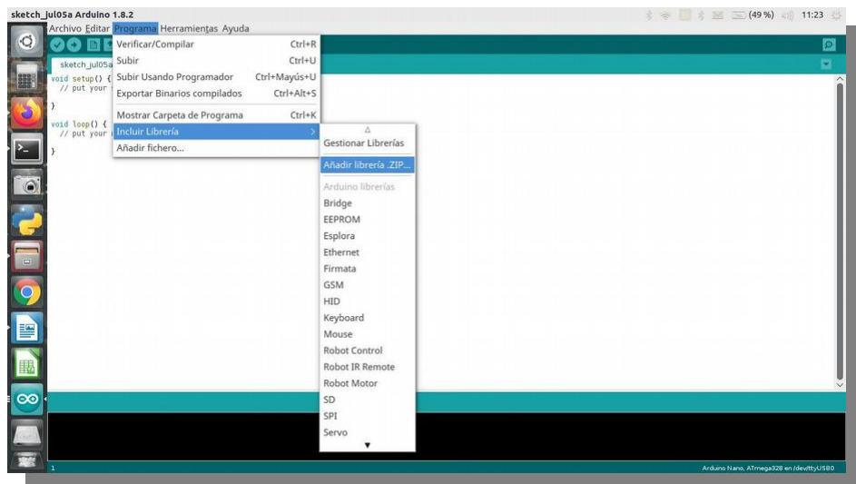
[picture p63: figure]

Hemos intentado implementar un software muy intuitivo, que incluye sus propios ejemplos para que el usuario novel pueda aprender por su cuenta el manejo del robot. En los próximos párrafos, de todos modos, daremos unas pinceladas a sus principales funcionalidades, que esperamos enriquecer con el tiempo si nuestro robot tiene la acogida que esperamos dentro de la comunidad educativa.
Iniciación a la programación con la librería <Masaylo.h>.

## Movimientos básicos

Una vez instalada la librería, el flujo de trabajo en todos nuestros programas seguirá el siguiente orden:
- Hacemos referencia a la librería mediante la directiva #include.
- Declaramos un objeto de la clase Masaylo
- En setup() inicializaremos dicho objeto mediante el método init(), indicando los pines de control de los motores izquierdo y derecho por este orden (MIA, MIB, MDA, MDB) que de acuerdo al pinout original significaría la secuencia 5, 6, 9 y 10.
- En su caso, inicializaremos también los sensores de infrarrojos (en conjunto o por separado), o el de medición de distancia por ultrasonidos.

69

- En el bucle loop() llamaremos a los métodos que necesitemos de la clase Masaylo de acuerdo al comportamiento que busquemos en el robot.

Métodos implementados para los movimientos básicos
En general, hemos mantenido para todos los métodos los mismos nombres que para las funciones desarrolladas a lo largo de este libro. Para los movimientos simples, de tipo todo/nada, los métodos designados son adelante(), atras(), izquierda(), derecha() y alto(). El código reseñado a continuación está incluido en los ejemplos de la librería, y reproduce la secuencia adelante (2 segundos), izquierda (1 segundo), atrás (2 segundos), derecha (1 segundo) y finalmente paro.

#include<Masaylo.h>

//Declaramos un objeto de la clase Masaylo, de nombre ejemplo m. Masaylo m;
//Configuracion
void setup() {
// Inicializamos el Masaylo:
m.init(5,6,9,10);
//Las funciones de movimiento son: adelante(), atras(), izquierda(), derecha() y alto() m.adelante();
delay(2000);
m.izquierda();
delay(1000);
m.atras();
delay(2000);
m.derecha();
delay(1000);
m.alto();
}
void loop() {
//No trabajamos en bucle en este programa }

70

## Movimientos de velocidad controlada mediante PWM

Al igual que en el trabajo por funciones, los métodos de la librería son los mismos que en los movimientos todo o nada, con la salvedad de que hay que pasar como parámetro un entero no mayor de 255 (velocidad máxima), y de valor mínimo alrededor de 120 (por debajo de esta barrera ya explicamos que el motor DC no funcionará).
El código de ejemplo que incluye la librería empieza con un movimiento hacia adelante de velocidad máxima, que va reduciendo paulatinamente a lo largo de 8 segundos, para finalmente parar y revertir su progreso hacia atrás con una velocidad creciente a lo largo de otros 8 segundos.

#include<Masaylo.h>

//Declaramos nuestro robot Masaylo m;

void setup() {
// Inicializamos el Masaylo:
m.init(5,6,9,10);
//Las funciones de movimiento son: adelante(velocidad), atras(velocidad), izquierda(velocidad), derecha(velocidad) y alto()

//La velocidad puede modularse entre los valores 120 (prácticamente parado) a 255 (velocidad máxima)

m.adelante(255);
delay(2000);
m.adelante(200);
delay(2000);
m.adelante(150);
delay(2000);
m.adelante(100);
delay(2000);
m.alto();
delay(2000);
m.atras(100);

71

delay(2000);
m.atras(150);
delay(2000);
m.atras(200);
delay(2000);
m.atras(255);
delay(2000);
m.alto();
}
void loop() {
//No trabajamos en bucle en este ejemplo.
}

## Uso del sensor de ultrasonidos. Robot salvaobstáculos

Si vamos a utilizar el sensor HC-SR04 o uno similar para detectar distancias, hay que declararlo después de inicializar el objeto de clase Masaylo mediante el método ultrasonidos, pasando como parámetros los pines Trigger y Echo (7 y 8 en el conexionado original). Si llamamos al método distancia() nos devolverá el valor detectado en cm en formato long.
El siguiente ejemplo lee la distancia al obstáculo y la pasa por el puerto serie (el hardware, no el BT):
#include<Masaylo.h>

Masaylo m;

void setup() {
// Inicializamos el Masaylo: m.init(5,6,9,10);
//Activamos sensor de ultrasonidos: m.ultrasonidos(7,8);
//Activamos el puerto serie Serial.begin(9600);
}

72

void loop() {
// La distancia medida por el HC-SR04 se remitirá en cm mediante una variable de tipo long long espacio=m.distancia();
Serial.print("Distancia: ");
Serial.println(espacio);
delay(500);
}

Combinando varios de los conceptos trabajados a lo largo de estos capítulos, podemos repetir el episodio del Masaylo que evita obstáculos que tenga delante (el código también está incluido entre los ejemplos de la librería):
#include <Masaylo.h>

Masaylo m;
void setup() {
//Declaramos un robot de clase Masaylo e inicializamos US m.init(5,6,9,10);
m.ultrasonidos(7,8);
}
void loop() {
//Medimos la distancia a un posible obstáculo
long espacio=m.distancia();
//Regulamos la velocidad según la distancia o retrocedemos if (espacio>40){
m.adelante(150);
}else if (espacio>20){
m.adelante(130);
}else{
m.alto();
//Damos tiempo al paro
delay(500);

73

m.atras();
delay(1000);
m.izquierda(150);
delay(500);
}
}

## Inicializando los sensores de infrarrojos

Los métodos para inicializar los sensores IR son tres:
- infrarrojos(pin sensor derecho, pin sensor izquierdo). Es el que nos parece más lógico utilizar.
- irIzq(pin sensor izquierdo) si sólo quisiéramos trabajar con este sensor.
- irDer(pin sensor derecho) si sólo quisiéramos el sensor IR derecho.
A su vez, se han desarrollado métodos de lectura que devuelven un valor de tipo booleano (verdadero/falso) según estemos buscando tonos blancos o negros:
Método | Comportamiento
nDerecha() | Devuelve true si el sensor derecho se encuentra el color negro
nIzquierda() | Devuelve true si el sensor izquierdo se encuentra el color negro
bDerecha() | Devuelve true si el sensor derecho se encuentra el color blanco
bIzquierda() | Devuelve true si el sensor derecho se encuentra el color negro

En el ejemplo lectorInfrarrojos utilizamos los dos primeros métodos para pasar por el puerto serie el estado de cada uno de los dos sensores.
#include<Masaylo.h>

//Declaramos el robot de clase Masaylo y las variables que recogerán la lectura de los sensores Masaylo m;

74

boolean izquierda, derecha; void setup() {
// Inicializamos el Masaylo: m.init(5,6,9,10);
//Activamos lectores de infrarrojos: m.infrarrojos(2,3);
//Activamos el puerto serie Serial.begin(9600);
}
void loop() {
/* Asignamos a las variables izquierda y derecha la lectura de las funciones nIzquierda y nDerecha (true para negro, false para blanco): */

izquierda=m.nIzquierda();
derecha=m.nDerecha();
Serial.print("Izquierda: "); if (izquierda){
Serial.print("negro");
}else{
Serial.print("blanco");
}
Serial.print("\t");
Serial.print("Derecha: "); if (derecha){
Serial.println("negro");
}else{
Serial.println("blanco");
}
delay(100);
}

75

Proponemos, por último, un replanteamiento del robot siguelíneas que veíamos al hablar de los sensores IR, de modo que el uso de esta librería simplifique el código (en la carpeta ejemplos, con el nombre sigueLineasNegras):
#include<Masaylo.h>

Masaylo m;
void setup() {
// Inicializamos el Masaylo: m.init(5,6,9,10);
//Activamos lectores de infrarrojos: m.infrarrojos(2,3);
}
void loop() {
//Declaramos un valor int que recoge las lecturas int lectura=leeSuelo();
/* La variable lectura nos dice qué hacer:
* 0: Vamos bien. Ambos sensores leen blanco
* 1: El sensor izquierdo "pisa la línea". Compensar a la izquierda * 2: El sensor derecho "pisa la línea". Compensar a la derecha
* 3: Ambos sensores leen negro. Error. Parar.
*/
switch (lectura){
case 0:
m.adelante(130);
break;
case 1:
m.izquierda(150);
break;
case 2:
m.derecha(150);
break;

76

case 3:
m.alto();
break;
}
}
int leeSuelo(){
//Variable local que recoge la lectura de los sensores int valor=0;
if (m.nIzquierda()){
valor+=1;
}
if (m.nDerecha()){
valor+=2;
}
return valor;
}

Epílogo | 77

# Epílogo

Masaylo es un robot muy querido para el que escribe estas últimas líneas. Fue su primer intento “serio”, años ha, de fabricar un robot de diseño propio, acorde con los medios y recursos que se pueden encontrar en un Aula-Taller de Tecnología en cualquier instituto público español de Educación Secundaria. Empezamos programando en ensamblador microcontroladores de tipo PIC. Después llegó Arduino, la maravillosa Arduino, que ha cambiado la metodología y los horizontes de tantos profesores y profesoras dedicados a la educación tecnológica. El gobierno razonable de motores de corriente continua omnipresentes en nuestros talleres sólo podía hacerse, al principio, implementando circuitos secundarios mediante transistores bipolares NPN que exigían siempre fuentes de alimentación aparte que complicaban mucho el trabajo, y que frecuentemente exigían un reacondicionamiento de la señal de control. Descubrimos poco después los circuitos integrados dedicados a este menester, como el L293DNE. Masaylo aparecía y desaparecía de mi mesa de trabajo, alternándose con otros proyectos y exigencias de mi oficio (de mi vida) como educador. En ocasiones me desesperaba. En otras me entusiasmaba. Podíamos olvidarlo durante meses, pero al final, de un modo o de otro, aparecía ahí, sobre un pupitre o un banco del taller, o en mi despacho, con su primer chasis de contrachapado mal cortado y los motorcillos DC pegados por algún alumno con dos sólidos goterones de pegamento termofusible.

En los últimos años, la universalización de Arduino ha mejorado exponencialmente la accesibilidad a todo tipo de circuitos de control y automatización, así como bajado su precio. Y algo fundamental: posibilitó la impresión 3D en los centros educativos, algo que hasta hacía sólo cuatro o cinco años (aún lo es ahora), parecía ciencia ficción. Software Open Source como FreeCAD ha posibilitado que cualquiera de nosotros, con un simple y viejo portátil, pueda imaginar y diseñar universos enteros en apenas unas horas.
El robot sobre el que estás leyendo siempre intentó dar la respuesta a tres problemas en la educación pública: conseguir un robot educativo a bajo costo y de fácil construcción en cualquier aula-taller de Tecnología, facilitar el aprendizaje de múltiples conceptos sobre Electrónica y Programación a través de ejercicios sencillos que el alumno pueda realizar en el tiempo material de una clase (no superior a los 45 minutos reales), y proporcionar a la comunidad, mediante la filosofía Open Source, una oportunidad de seguir creciendo al poder compartir, distribuir y modificar libremente tanto los diseños como las piezas en STL y el software del Masaylo que aquí ponemos a vuestra disposición.
No quiero terminar este texto sin agradecer con todo mi corazón su tarea como ingenieros y divulgadores tanto a David Cuartielles, codiseñador del concepto de la tarjeta Arduino como a Juan González, Obijuan, que nos ha inspirado a tantos para iniciar nuestros caminos en la impresión y el diseño 3D.
¡Siempre creciendo, siempre aprendiendo!. Cultura maker.
Antonio Gómez García
www.aprendizdetecnologo.com

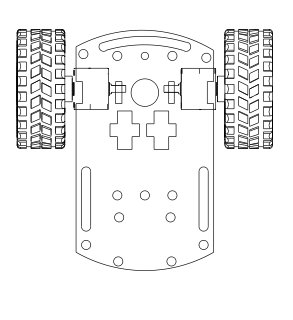
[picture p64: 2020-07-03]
Images/montaje/vistaBase.png

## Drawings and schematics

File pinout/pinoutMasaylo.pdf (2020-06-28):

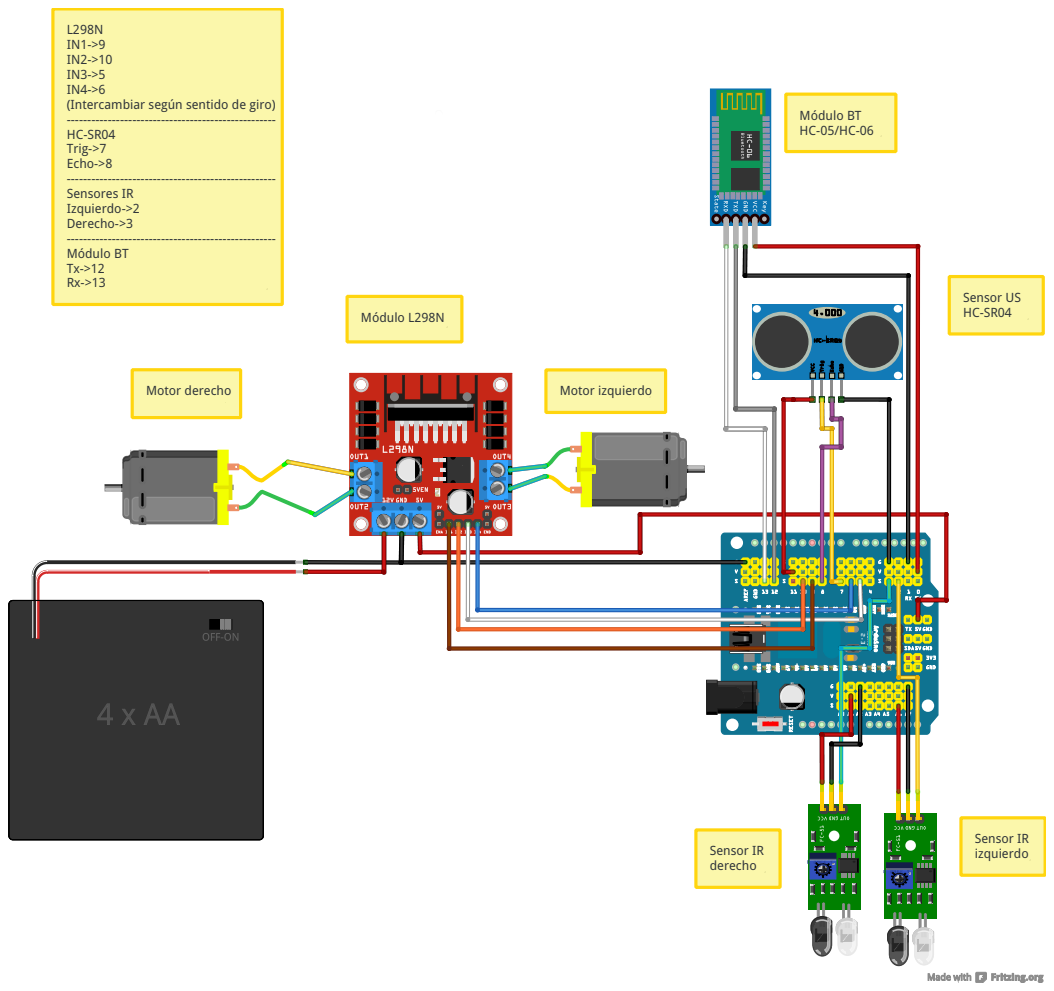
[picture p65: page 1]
Sensor IR derecho; Sensor IR izquierdo; Motor derecho; Motor izquierdo; Módulo BT HC-05/HC-06; Sensor US; HC-SR04 ódulo L298N; L298N IN1->9 IN2->10 IN3->5 IN4->6 (Intercambiar según sentido de giro) --------------------------------------------------- HC-SR04 Trig->7 Echo->8 --------------------------------------------------- Sensores IR Izquierdo->2 Derecho->3 --------------------------------------------------- Módulo BT Tx->12 Rx->13

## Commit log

2015-03-06 Mis primeros pasos con FreeCad
    [CASAGRANDE.fcstd, NOMBRELOLA.fcstd, NOMBRELOLA.stl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]
2015-04-15 Ensayo pinza
    [ensayoPinza.FCStd]
2015-04-15 Otra pinza
    [Servo_gripper.dxf, back.STL, bottom.STL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]
2020-06-25 Borrando archivos antiguos...
    [CASAGRANDE.fcstd, NOMBRELOLA.fcstd, NOMBRELOLA.stl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]
2020-06-25 Primeros pasos con la versión impresa en plástico
    [BASE.stl, SEGUNDOPISO.stl, SEPARADOR(x6).stl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]
2020-06-26 Cambios en diseño
    [ruedaLoca(inexacta).fcstd]
2020-06-28 Añadido pinout
    [pinoutMasaylo.fzz]
2020-06-30 Tutorial de montaje
    [BASE.stl, SEGUNDOPISO.stl, SEPARADOR(x6).stl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]
2020-07-01 Librería de control del Masaylo
2020-07-01 Inicio de manual
2020-07-01 Rediseñando soporte US
    [SOPORTEUS.stl, soporteUS.FCStd]
2020-07-01 Updating soporte US
    [SOPORTEUS.stl, soporteUS.FCStd]
2020-07-02 Updating soporteUS
    [SOPORTEUS.stl, portapilasChapucero.stl, separaRueda(x4).stl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]
2020-07-03 Updating both code and manual
    [soporteUS.FCStd]
